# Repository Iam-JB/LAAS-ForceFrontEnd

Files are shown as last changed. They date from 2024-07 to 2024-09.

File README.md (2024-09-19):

# LAAS-ForceFrontEnd

Electronics development to acquire and process force measurements produced by an actuator in order to achieve torque control.

Here you will find the technical review : Technical Review and the poster here : Poster

Files sumarry :  
   ADS1235EVM.kicad_sch   KiCAD Schematic of our own acquisition PCB  
   ADS1235EVM.kicad_pcb   KiCAD PCB Routing of our own acquisition PCB  
   ForceDetection.ino       Code in order to flash Raspberry Pi Pico  
   ExtractData.py               Parceur that extracts force value from an external file ('xxx.bin') and plots through MatPlotLib  
   RealTimeParceur.py       Parceur that extracts data directly from serial port and plots through PlotJuggler

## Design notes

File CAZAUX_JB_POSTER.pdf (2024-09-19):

CONTEXTE
L’équipe Gepetto du LAAS CNRS à Toulouse travaille à la conception, à la génération de mouvement et au contrôle de robots à jambes (humanoides et quadrupède). Pour des besoins de retour d’effort et d’interaction souple avec l’environnement, les articulations des robots sont généralement équipées de capteurs de couple à base de jauge de contraintes. Une fois conditionnées et filtrées, les mesures de couples sont utilisées comme retour d’état du contrôleur du robot. L’équipe Gepetto juge essentiel la qualité de ces mesures d’effort dont dépend la stabilité et la robustesse de l’exécution des taches robotiques (locomotion, manipulation).
Ce stage vise à développer l’électronique pour acquérir et traiter les mesures de forces produites par un actionneur, afin de l’asservir en couple.

## MESURE DE LA FORCE APPLIQUÉE PAR UN ACTIONNEUR POUR LA RÉALISATION D’UN ASSERVISSEMENT MOTEUR EN COUPLE

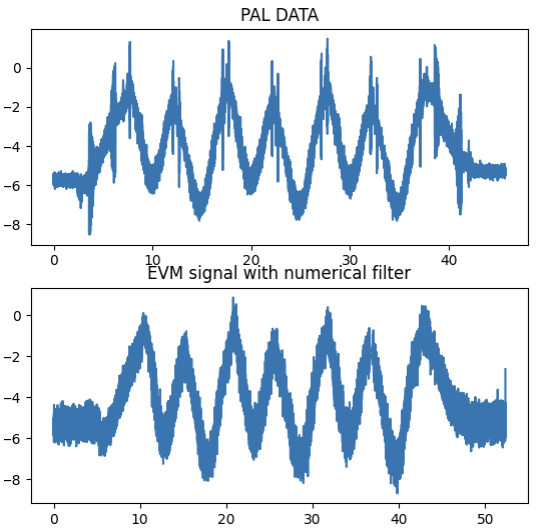
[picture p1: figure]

Jean-Baptiste Cazaux, 4°AE-SE

Mouvement des systèmes anthropomorphes

CONTRIBUTEURS
Thomas Flayols

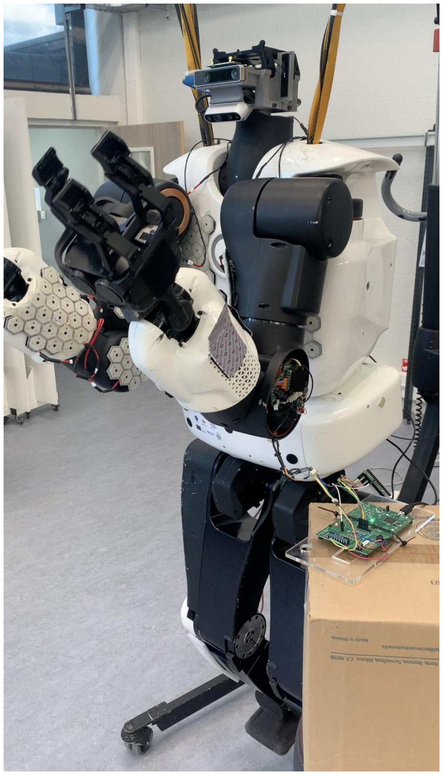
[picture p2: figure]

Jérome Manhes | Stéphane Grondin | Pierre Fernbach
CONCLUSION & PERSPECTIVES | APPORTS PERSONNELS

PROJET
Chaîne d’acquisition ratiométrique d’un pont de Wheatstone

### 1. Conception

### 2. Réalisation

### 3. Caractérisation

https://github.com/Iam-JB/LAAS-ForceFrontEnd

Recherche d’une solution générique permettant l’amplification différentielle, le filtrage et la conversion analogique numérique.
Schématique et routage de la carte d’acquisition.

Formation câblage et wrappage à l’atelier électronique et soudure de notre PCB avec des composants passifs en 0402.
Réalisation de parseurs en python et code pour commander divers microcontrôleurs (RPi 400, Pi Pico, ESP32).

Évaluation du niveau de bruit entre PCB et EVM (SNR, FFT).
Évaluation de la vitesse de communication UART. Comparaison avec l’amplificateur de PAL Robotics. Réalisation d’un filtre numérique et mise à l’échelle.

L’objectif du stage a été atteint avec l’implémentation d’une commande simple sur TALOS, servant de preuve de concept au fonctionnement de la carte d’acquisition.

Perspectives: Excitation AC et NTC pour le pont de jauges.

Ce stage m’a permis de me familariser avec le monde de la recherche ainsi que de mener à bien, en autonomie, un projet dans sa globalité.

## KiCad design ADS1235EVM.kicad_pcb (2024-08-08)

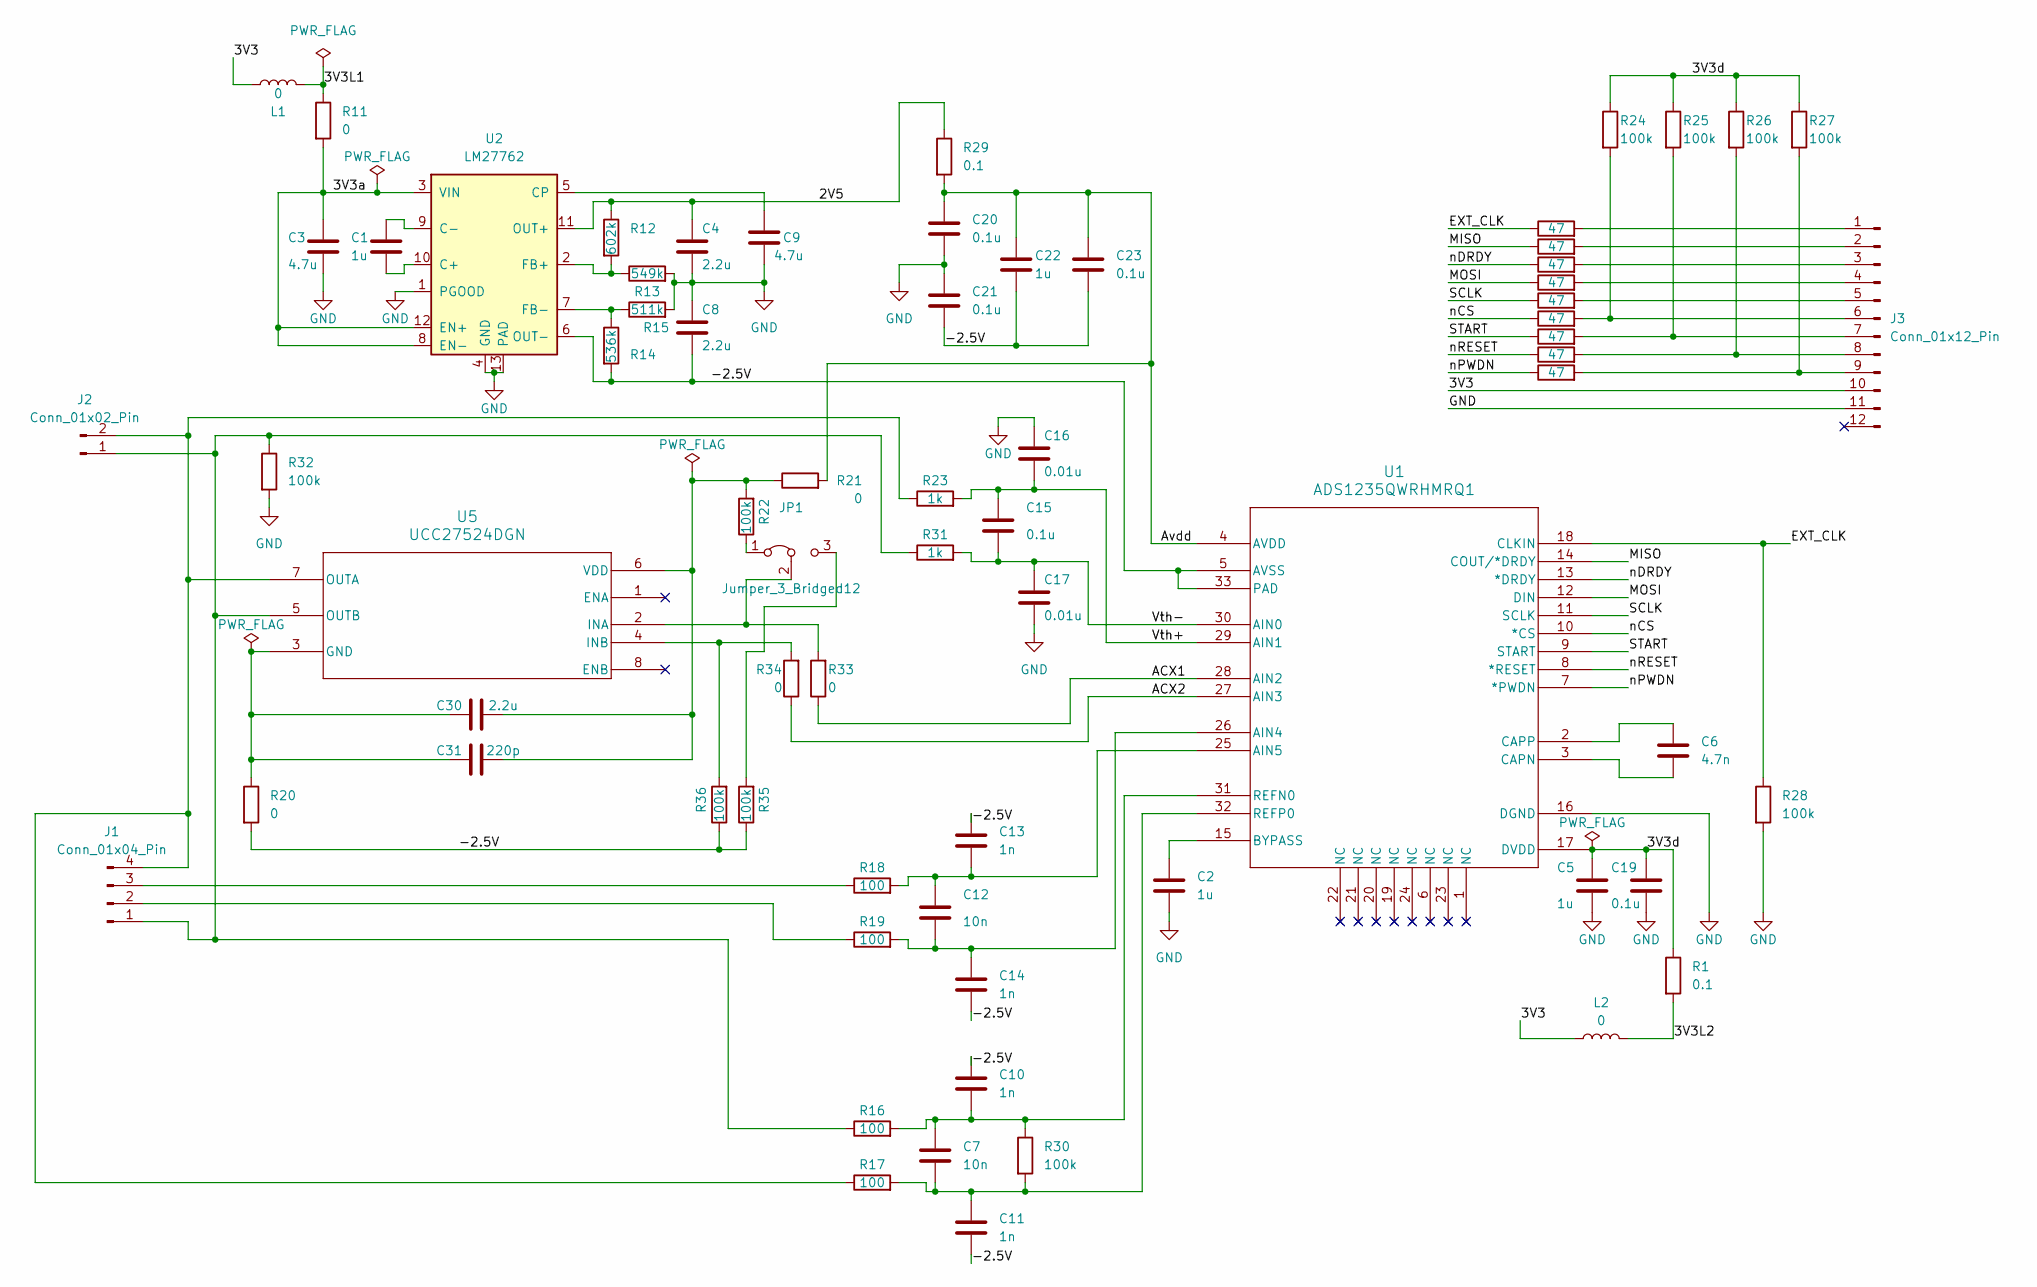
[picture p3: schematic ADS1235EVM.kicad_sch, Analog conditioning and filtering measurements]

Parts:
C1, C2, C5, C22: 1u; C_0402_1005Metric
C3, C9: 4.7u; C_0402_1005Metric
C4, C8, C30: 2.2u; C_0402_1005Metric
C6: 4.7n; C_0402_1005Metric
C7, C12: 10n; C_0402_1005Metric
C10, C11, C13, C14: 1n; C_0402_1005Metric
C15, C19, C20, C21, C23: 0.1u; C_0402_1005Metric
C16, C17: 0.01u; C_0402_1005Metric
C31: 220p; C_0402_1005Metric
J1: Conn_01x04_Pin; Hirose_DF13-04P-1.25DSA_1x04_P1.25mm_Vertical
J2: Conn_01x02_Pin; Hirose_DF13-02P-1.25DSA_1x02_P1.25mm_Vertical
J3: Conn_01x12_Pin; PinHeader_2x06_P2.54mm_Vertical
JP1: Jumper_3_Bridged12; SolderJumper-3_P1.3mm_Open_RoundedPad1.0x1.5mm
L1, L2: 0; L_0402_1005Metric
R1, R29: 0.1; R_0402_1005Metric
R2, R3, R4, R5, R6, R7, R8, R9, R10: 47; R_0402_1005Metric
R11, R20, R21, R33, R34: 0; R_0402_1005Metric
R12: 602k; R_0402_1005Metric
R13: 549k; R_0402_1005Metric
R14: 536k; R_0402_1005Metric
R15: 511k; R_0402_1005Metric
R16, R17, R18, R19: 100; R_0402_1005Metric
R22, R24, R25, R26, R27, R28, R30, R32, R35, R36: 100k; R_0402_1005Metric
R23, R31: 1k; R_0402_1005Metric
U1: ADS1235QWRHMRQ1; RHM0032A_VQFNP_TEX
U2: LM27762; WSON-12-1EP_3x2mm_P0.5mm_EP1x2.65_ThermalVias
U5: UCC27524DGN; DGN8

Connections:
/2V5: C4.1, R12.1, R29.1, U2.11 (OUT+)
/3V3: J3.10, L1.1, L2.1
/3V3L1: L1.2, R11.1
/3V3L2: L2.2, R1.2
/3V3a: C3.1, R11.2, U2.3 (VIN), U2.8 (EN-), U2.12 (EN+)
/3V3d: C5.1, C19.1, R1.1, R24.1, R25.1, R26.1, R27.1, U1.17 (DVDD)
/-2.5V: C8.2, C10.1, C11.2, C13.1, C14.2, C21.2, C22.2, C23.2, R14.2, R20.2, R35.1, R36.1, U1.5 (AVSS), U1.33 (PAD), U2.6 (OUT-)
/ACX1: R33.1, U1.28 (AIN2)
/ACX2: R34.1, U1.27 (AIN3)
/Avdd: C20.1, C22.1, C23.1, R21.2, R29.2, U1.4 (AVDD)
/EXT_CLK: R7.1, R28.1, U1.18 (CLKIN)
/MISO: R3.1, U1.14 (COUT/*DRDY)
/MOSI: R4.1, U1.12 (DIN)
/SCLK: R5.1, U1.11 (SCLK)
/START: R9.1, U1.9 (START)
/Vth+: C15.1, C16.2, R23.2, U1.29 (AIN1)
/Vth-: C15.2, C17.1, R31.2, U1.30 (AIN0)
/nCS: R6.1, U1.10 (*CS)
/nDRDY: R2.1, U1.13 (*DRDY)
/nPWDN: R10.1, U1.7 (*PWDN)
/nRESET: R8.1, U1.8 (*RESET)
GND: C2.2, C3.2, C4.2, C5.2, C8.1, C9.2, C16.1, C17.2, C19.2, C20.2, C21.1, J3.11, R13.2, R15.2, R28.2, R32.2, U1.16 (DGND), U2.1 (PGOOD), U2.4 (GND), U2.13 (PAD)
unnamed: J1.1, J2.1, R16.1, R31.1, R32.1, U5.5 (OUTB)
unnamed: J1.2, R19.1
unnamed: J1.3, R18.1
unnamed: J1.4, J2.2, R17.1, R23.1, U5.7 (OUTA)
unnamed: J3.1, R7.2
unnamed: J3.2, R3.2
unnamed: J3.3, R2.2
unnamed: J3.4, R4.2
unnamed: J3.5, R5.2
unnamed: J3.6, R6.2, R24.2
unnamed: J3.7, R9.2, R25.2
unnamed: J3.8, R8.2, R26.2
unnamed: J3.9, R10.2, R27.2
unnamed: JP1.1 (A), R22.1
unnamed: JP1.3 (B), R35.2
unnamed: JP1.2 (C), R33.2, U5.2 (INA)
unnamed: C12.2, C14.1, R19.2, U1.26 (AIN4)
unnamed: C12.1, C13.2, R18.2, U1.25 (AIN5)
unnamed: C2.1, U1.15 (BYPASS)
unnamed: C6.1, U1.3 (CAPN)
unnamed: C6.2, U1.2 (CAPP)
unnamed: C7.1, C10.2, R16.2, R30.1, U1.31 (REFN0)
unnamed: C7.2, C11.1, R17.2, R30.2, U1.32 (REFP0)
unnamed: C1.2, U2.10 (C+)
unnamed: C1.1, U2.9 (C-)
unnamed: C9.1, U2.5 (CP)
unnamed: R12.2, R13.1, U2.2 (FB+)
unnamed: R14.1, R15.1, U2.7 (FB-)
unnamed: C30.1, C31.1, R20.1, U5.3 (GND)
unnamed: R34.2, R36.2, U5.4 (INB)
unnamed: C30.2, C31.2, R21.1, R22.2, U5.6 (VDD)

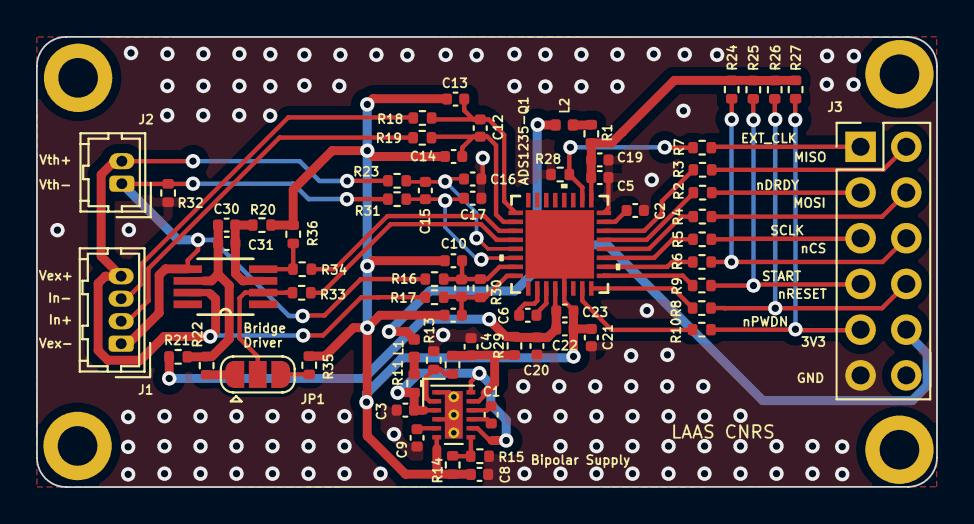
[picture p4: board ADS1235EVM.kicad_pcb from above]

Board: 2 copper layers, 50.0 x 25.0 mm, 69 parts (0 on the bottom side), 53 nets.

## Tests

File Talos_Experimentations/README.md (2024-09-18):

In this folder you will find all the results concerning differents experimentations of TALOS's left elbow torque sensor.

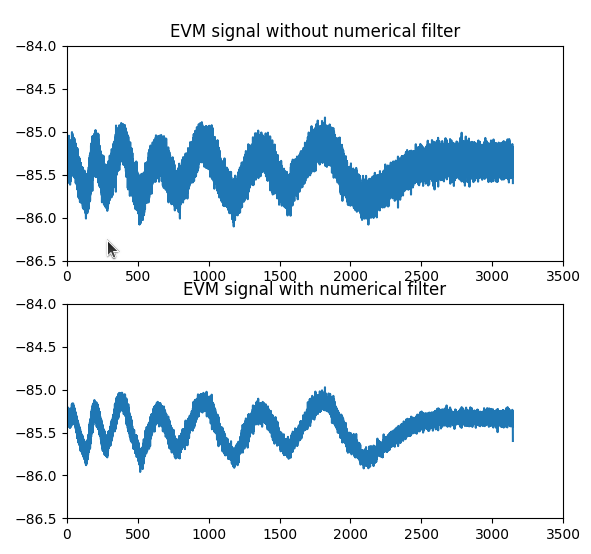
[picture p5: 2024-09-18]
Talos_Experimentations/EVM_with&withoutFilter+2kSAMPL.png

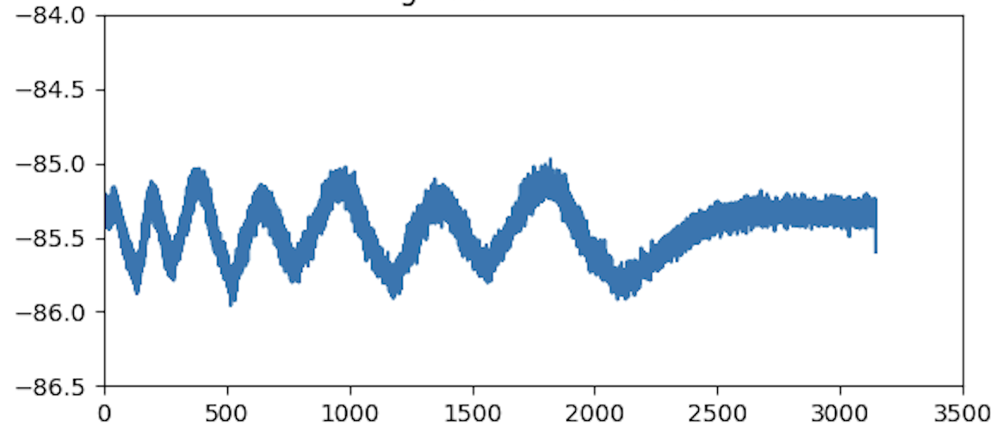
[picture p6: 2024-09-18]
Talos_Experimentations/EVM_FIltering+2kHzSampling.png

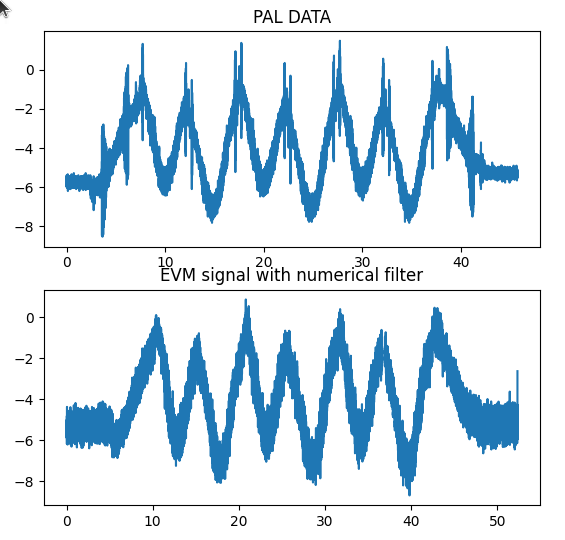
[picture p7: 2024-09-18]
Talos_Experimentations/comparaisonWithPAL_scaled.png

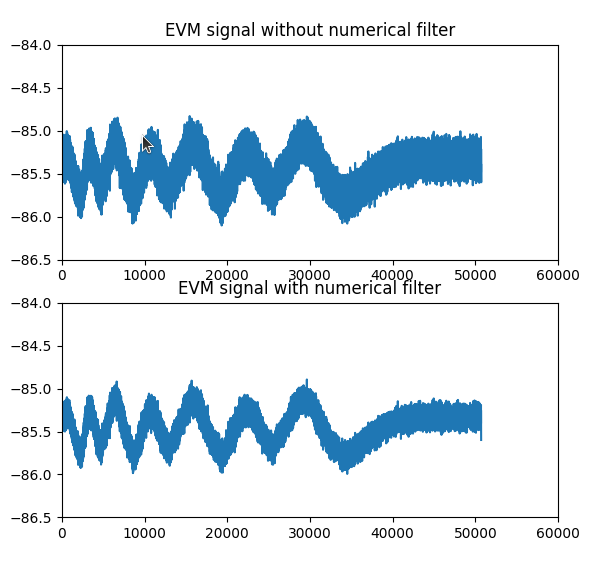
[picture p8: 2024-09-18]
Talos_Experimentations/EVM_with&withoutFilter.png

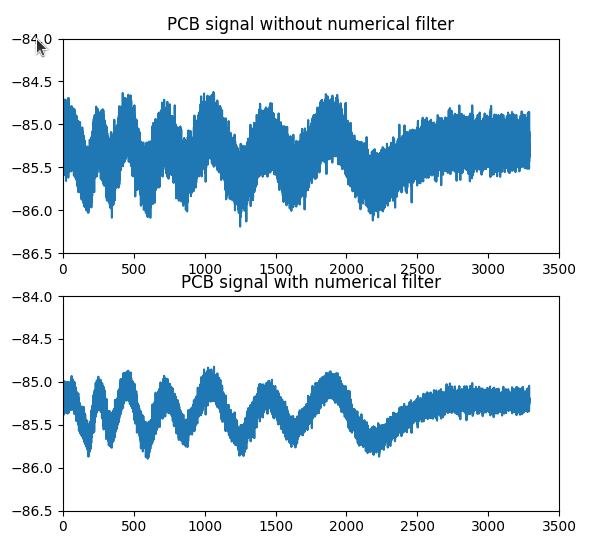
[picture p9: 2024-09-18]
Talos_Experimentations/PCB_with&withoutFilter+2kSAMPL.png

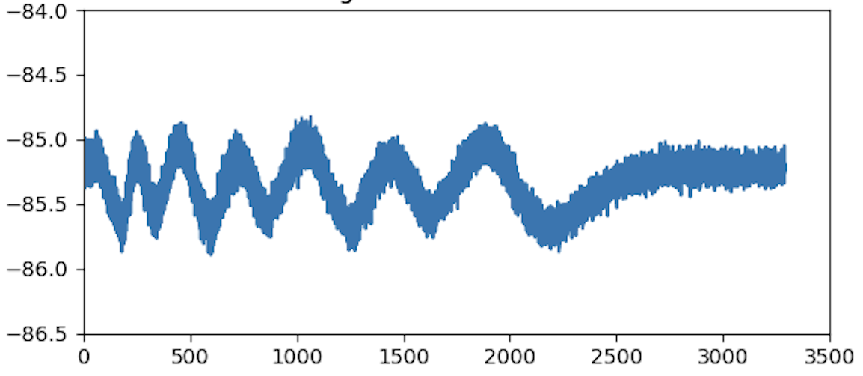
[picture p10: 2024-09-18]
Talos_Experimentations/PCB_Filtering+2kHzSampling.png

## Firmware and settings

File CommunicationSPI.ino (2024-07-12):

// For televersing the arduino code on the card
//    --> In order to solve the ttyACM0 probelm, you have to double-click the arduino reset button and then it goes fine

// I am currently blocked at the isTransferDone function
// @TO DO Check what SERCOM is necessary for implementing SPI on the Arduino Nano 33 IoT
//        Learn more about the Direct Access Memory (DMA)


#include <SPI.h>
#include <Adafruit_ZeroDMA.h>
#include "utility/dma.h"
#include "wiring_private.h" // pinPeripheral() function

#define nCS 8       // Chip Select
#define MOSI 11     // Master To Slave
#define MISO 12     // Slave To Master
#define SCLK 13     // Serial Clock

#define START 14
#define nDRDY 15
#define nPWDN 16
#define nRESET 17

SPIClassSAMD mySPI(
  &sercom1,
  12,
  13,
  11,
  SPI_PAD_0_SCK_1,
  SERCOM_RX_PAD_3
);

// MY VARIABLES

long ADC_VALUE;
long CLK = 7372800;      // 7.3728 MHz

Adafruit_ZeroDMA myDMA;
ZeroDMAstatus    stat;   // DMA status codes returned by some functions
DmacDescriptor *desc;    // DMA descriptor address

#define DATA_LENGTH 3
uint8_t receiveBuffer[DATA_LENGTH];
volatile bool isTransferDone = false;

// Callback for end of DMA transfer
void dmaCallback(Adafruit_ZeroDMA *dma) {
  (void) dma ;
  isTransferDone = true ;
  Serial.println("CALLBACK");
}

// Interrupt Service Routine for nDRDY
void nDRDY_ISR() {
  Serial.println("ENTRERING DATA READY HANDLER");

  digitalWrite(nCS, LOW);
  
  while (!isTransferDone) {                  // I am blocked here !! The callback function is never called
    
    if (myDMA.isActive()) {
      Serial.println("DR HANDLER : The transfer is still being processed...");
    } else {
      Serial.println("DR HANDLER : The transfer isn't in processing mode");
    }

    // print the register in order to know if it is my configuration that isn't good or smthing else
    
    delay(1000000);
  }
  Serial.println("DR HANDLER : The transfer is finally finished !");

  // Process received data
  ADC_VALUE = 0;
  for (int i = 0; i < DATA_LENGTH; i++) {
    ADC_VALUE = (ADC_VALUE << 8) | receiveBuffer[i];
  }

  Serial.print("ADC VALUE: ");
  Serial.println(ADC_VALUE);

  isTransferDone = false;

  stat = myDMA.free();
  if (stat != DMA_STATUS_OK) {
    Serial.println("DMA free has failed");
  }

  stat = myDMA.allocate();
  if (stat != DMA_STATUS_OK) {
    Serial.println("DMA allocate has failed");
    myDMA.printStatus(stat);
  }
  
  stat = myDMA.startJob();
  if (stat != DMA_STATUS_OK) {
    Serial.println("DMA start has failed");
    myDMA.printStatus(stat);
  }
  
  digitalWrite(START, HIGH);                // Start or restart a new ADC conversion
  digitalWrite(nCS, HIGH);
}


// MY FUNCTIONS

void initArduinoNano() {
  pinMode(nCS,    OUTPUT);
  pinMode(MOSI,   OUTPUT);
  pinMode(MISO,   INPUT );
  pinMode(SCLK,   OUTPUT);
  pinMode(START,  OUTPUT);
  pinMode(nRESET, OUTPUT);
  pinMode(nPWDN,  OUTPUT);
  pinMode(nDRDY,  INPUT );

  pinPeripheral(MOSI, PIO_SERCOM);
  pinPeripheral(MISO, PIO_SERCOM);
  pinPeripheral(SCLK, PIO_SERCOM);
}

int readRegister(byte address) {
  byte command = 0x20 + (address & 0x1F);  // RREG is 20h + rrh where rrh is a 5-bit register address
  digitalWrite(nCS, LOW);                                   
  mySPI.transfer(command);                   // BYTE 1 (DIN : 0x20 + 5-bit register address, DOUT : 0xFF)
  mySPI.transfer(0xFF);                      // BYTE 2 (DIN : Arbitary, DOUT : Echo byte 1)
  int value = mySPI.transfer(0x00);          // BYTE 3 (DIN : 0x00, DOUT : Register data)
  digitalWrite(nCS, HIGH);
  return value;
}

void writeRegister(byte address, int value) {
  digitalWrite(nCS, LOW);  
  byte command = 0x40 + address;
  mySPI.transfer(command);                // BYTE 1 (DIN : 0x40 + 5-bit register address, DOUT : 0xFF)
  mySPI.transfer(value);                  // BYTE 2 (DIN : Register data, DOUT : Echo byte 1)
  digitalWrite(nCS, HIGH);
}

void setup() {
  Serial.begin(2000000);
  while(!Serial);
  Serial.println("HELLO WORLD");
  initArduinoNano();

  mySPI.begin(); // Initialize the SPI library
  mySPI.beginTransaction(SPISettings(8000000, MSBFIRST, SPI_MODE1));

  digitalWrite(nCS, HIGH); // Communication disable
  digitalWrite(nRESET, HIGH);
  digitalWrite(nPWDN, HIGH);

  // OPTIONAL : AC EXCITATION
  
//  byte address = 0x03 ;
//  byte value = readRegister(address);

//  value &= ~((0b11) << 5); // Clear the bits of CHOP[1:0]
//  value |= (0b10 << 5);    // 2-wire AC-bridge excitation mode

//  writeRegister(address,value);

  // DATA RATE CONFIGURATION
  byte addressDR = 0b00010;
  int valueDR = readRegister(addressDR);
  valueDR = 0b01100100;
  writeRegister(addressDR, valueDR);

  // PGA CONFIGURATION
  byte addressPGA = 0b10000;
  int valuePGA = readRegister(addressPGA);
  valuePGA = 0b10000111;  // Gain of 128
  writeRegister(addressPGA, valuePGA);

  // INPUT MUX CONFIGURATION
  byte addressMUX = 0b10001;
  int valueMUX = readRegister(addressMUX);
  valueMUX = 0b01111000;
  writeRegister(addressMUX, valueMUX);

  // REF CONFIGURATION
  byte addressREF = 0b00110;
  int valueREF = readRegister(addressREF);
  valueREF = 0b00001010;
  writeRegister(addressREF, valueREF);

  // OFFSET CALIBRATION
  writeRegister(0x07, 0x00);
  writeRegister(0x08, 0x00);
  writeRegister(0x09, 0x00);

  // FULL SCALE CALIBRATION
  writeRegister(0x0A, 0x00);
  writeRegister(0x0B, 0x00);
  writeRegister(0x0C, 0x40);


  // Direct Access Memory (DMA)
  
  stat = myDMA.allocate();
  if (stat != DMA_STATUS_OK) {
    Serial.print("Allocate : ");
    myDMA.printStatus(stat);
  }

    // DMA Configuration for SPI    
             
        // SERCOM4 is the 'native' SPI SERCOM on most M0 boards but section 6. mentions that according to the Arduino pinout,
        // the SERCOM that corresponds is the SERCOM1
        
  myDMA.setTrigger(SERCOM1_DMAC_ID_RX);       // To receive from SPI
  Serial.print("TRIGGER bit : ");
  Serial.println(DMAC->CHCTRLB.bit.TRIGSRC);
  myDMA.setAction(DMA_TRIGGER_ACTON_BEAT);
  Serial.print("ACT ON bit : ");
  Serial.println(DMAC->CHCTRLB.bit.TRIGACT);

  desc = myDMA.addDescriptor(
    (void *)(&SERCOM1->SPI.DATA.reg),   // SRC
    receiveBuffer,                      // DEST
    DATA_LENGTH,                        // length
    DMA_BEAT_SIZE_BYTE,                 // bytes
    false,                              // no incrementation of SRC address
    true                                // incrementation of DEST address
  );

    // Fill the buffer with incrementing bytes
//  for (uint32_t i=0; i<DATA_LENGTH; i++) {       // Does that is really usefull here ? Why's that ?
//    receiveBuffer[i]=i;
//  }

  myDMA.loop(false);
  myDMA.setCallback(dmaCallback, DMA_CALLBACK_TRANSFER_DONE);            // The second argument (DMA_CALLBACK_TRANSFER_DONE) is not especially necessary here as it is set by default
  myDMA.setPriority(DMA_PRIORITY_3);         // Set the highest to DMA
 
    // Enable global interrupts
  NVIC_SetPriority(DMAC_IRQn, 10);           // Set the Nested Vector Interrupt Controller (NVIC) priority for the DMAC to 0 (highest) 
  NVIC_EnableIRQ(DMAC_IRQn);
  
    // Attach interrupt to nDRDY pin
  attachInterrupt(digitalPinToInterrupt(nDRDY), nDRDY_ISR, FALLING);

  stat = myDMA.startJob();
  if (stat != DMA_STATUS_OK) {
    Serial.println("DMA start has failed");
    myDMA.printStatus(stat);
  }

  digitalWrite(nCS, LOW);             // Enable communication
  digitalWrite(START, HIGH);          // ADC start
  Serial.println("I've been here");
}

void loop() {
  // Nothing here, done by IT
  
  Serial.println(".");
  
//  Serial.print("enable bit : ");
//  Serial.println(DMAC->CHCTRLA.bit.ENABLE);
//
//  Serial.print("Transfer Complete bit : ");
//  Serial.println(DMAC->CHINTFLAG.reg);
//
//  Serial.print("Chanel causing IT : ");
//  Serial.println(DMAC->INTPEND.bit.ID);
}

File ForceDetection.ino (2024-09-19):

#include <stdio.h>
#include <SPI.h>

// Jean-Baptiste CAZAUX - Tuesday 16 July
// https://github.com/Iam-JB/LAAS-ForceFrontEnd

// GPIOs DEFINITION
const int nCS = 17;
const int START = 20;
const int nDRDY = 21;
const int nPWDN = 26;
const int nRESET = 22;

// Buffers
const int SYNC = 0x31;
uint16_t counter = 0x0000;      // Counter 16 bits
uint8_t tabToBeSendUART[6];

void initPiPico() {
    // Initialize GPIO pins
    pinMode(nCS, OUTPUT);
    pinMode(START, OUTPUT);
    pinMode(nRESET, OUTPUT);
    pinMode(nPWDN, OUTPUT);
    pinMode(nDRDY, INPUT);

    // Initialize SPI
    SPI.begin();
    SPI.beginTransaction(SPISettings(4000000,MSBFIRST,SPI_MODE1));
}

// READ ADS1235Q1's REGISTERS
uint8_t readRegister(uint8_t address) {
    uint8_t command = 0x20 + (address & 0x1F); // RREG is a 0x20 + rrh, where rrh is a 5-bit register
    digitalWrite(nCS, LOW);
    SPI.transfer(command);
    SPI.transfer(0xFF);
    uint8_t value = SPI.transfer(0x00);
    digitalWrite(nCS, HIGH);
    return value;
}

// WRITE ADS1235Q1's REGISTERS
void writeRegister(uint8_t address, uint8_t value) {
    digitalWrite(nCS, LOW);
    uint8_t command = 0x40 + (address & 0x1F); // WREG is a 0x40 + rrh, where rrh is a 5-bit register
    SPI.transfer(command);
    SPI.transfer(value);
    digitalWrite(nCS, HIGH);
}

void setupMain() {
    // INIT
    Serial.begin();   // No need to specify serial speed for Pi Pico due to virtual UART
    while(!Serial);
    initPiPico();

    digitalWrite(nCS, HIGH);
    digitalWrite(nRESET, HIGH);
    digitalWrite(nPWDN, HIGH);
    digitalWrite(START, LOW);

    // DC-EXCITATION CONFIGURATION
    uint8_t addressEXC = 0b00011;
    uint8_t valueDC = 0b00001001;  // DC-EXCITATION and conversion start delay = 1.16ms (cf. datasheet)
    writeRegister(addressEXC, valueDC);

    // DATA RATE CONFIGURATION
    uint8_t addressDR = 0b00010;
//    uint8_t valueDR = 0b01100011;  // 7200 SPS & sinc1 (-3dB cutoff frequency at 2300Hz)
//    uint8_t valueDR = 0b01100011;  // 7200 SPS & sinc2 (-3dB cutoff frequency at 1960Hz)
//    uint8_t valueDR = 0b01100011;  // 7200 SPS & sinc3 (-3dB cutoff frequency at 1740Hz)
    uint8_t valueDR = 0b01100011;  // 7200 SPS & sinc4 (-3dB cutoff frequency at 1580Hz)
    writeRegister(addressDR, valueDR);

    // PGA CONFIGURATION
    uint8_t addressPGA = 0b10000;
    uint8_t valuePGA = 0b10000111;  // Gain of 128
    writeRegister(addressPGA, valuePGA);

    // INPUT MULTIPLEXER CONFIGURATION
    uint8_t addressMUX = 0b10001;
    uint8_t valueMUX = 0b01111000;  // AIN4(+) and AIN5(-)
    writeRegister(addressMUX, valueMUX);

    // REFERENCE CONFIGURATION
    uint8_t addressREF = 0b00110;
    uint8_t valueREF = 0b00001010;
    writeRegister(addressREF, valueREF);

    // USER CALIBRATION
       // OFCAL
    // writeRegister(0x07, 0x00); // Follow the user calibration procedure (cf. datasheet)
    // writeRegister(0x08, 0x00);
    // writeRegister(0x09, 0x00);
    writeRegister(0x07, 0x7D); // Follow the user calibration procedure (cf. datasheet)
    writeRegister(0x08, 0x27);
    writeRegister(0x09, 0x04);

      // FSCAL
    writeRegister(0x0A, 0x00); // Follow the user calibration procedure (cf. datasheet)
    writeRegister(0x0B, 0x00);
    writeRegister(0x0C, 0x40);
  //  writeRegister(0x0A, 0xCC);
  //  writeRegister(0x0B, 0xCC);
  //  writeRegister(0x0C, 0x3C);
}


void myCallback() {
    uint32_t ADC_VALUE = 0;
    
    digitalWrite(nCS, LOW);
    SPI.transfer(0x12);
    SPI.transfer(0xFF);
    uint8_t MSB = SPI.transfer(0x00);
    uint8_t MIDSB = SPI.transfer(0x00);
    uint8_t LSB = SPI.transfer(0x00);
    digitalWrite(nCS, HIGH);

    int data[3] = {MSB,MIDSB,LSB};
    for (int i = 0 ; i <= 2 ; i++){
      ADC_VALUE = (ADC_VALUE << 8) | data[i];
    }
    uint32_t ADC_VALUE_DATA = ADC_VALUE & 0x7FFFFF ;
    uint32_t ADC_VALUE_SIGN = (ADC_VALUE & 0x800000) >> 23 ;

    // FORMATING AS SYNC | COUNTER | FORCE_VALUE
    counter++;
    uint8_t MSBcounter = (counter & 0xFF00) >> 8 ;
    uint8_t LSBcounter = counter & 0x00FF ;
    
    tabToBeSendUART[0] = SYNC ;
    tabToBeSendUART[1] = MSBcounter ;
    tabToBeSendUART[2] = LSBcounter ;
    tabToBeSendUART[3] = MSB ;
    tabToBeSendUART[4] = MIDSB ;
    tabToBeSendUART[5] = LSB ;

    Serial.write(tabToBeSendUART,6);
    Serial.flush();

    if (counter >= 0xFFFF) { // Not really needed here as counter is defined as a uint16_t
      counter = 0x0000;
    }

}

void setup() {
    setupMain();
    digitalWrite(START, HIGH); // Start conversion acquisitions
}

void loop() {
  while (1) {
    while(!digitalRead(nDRDY));
    while(digitalRead(nDRDY));
    myCallback();
  }
}

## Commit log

2024-06-19 Schematics - All components included
    [PrincipleSchematicV3.kicad_sch]
2024-06-19 Schematics - Add of jumpers to handle AC or DC excitation
    [PrincipleSchematicV4.kicad_sch]
2024-06-21 Double Side Routing - First version
    [PrincipleSchematicV4.kicad_pcb]
2024-06-21 Double Side Routing - Second version
    It is a more compact PCB with the add of a bottom ground surface
    [PrincipleSchematicV4bis.kicad_pcb]
2024-06-24 Project - Both the schematic and routing files included
2024-06-24 Add schematic & routing files
    [ADS1235EVM.kicad_pcb, ADS1235EVM.kicad_sch]
2024-06-24 Routing - Add of 2 ferrites bead for power
    [ADS1235EVM.kicad_pcb]
2024-06-25 Routing - Tie unused analog inputs to Avdd
    [ADS1235EVM.kicad_pcb]
2024-06-25 Routing - Components placement correction + DRC OK
    [ADS1235EVM.kicad_pcb]
2024-06-25 Add of .kicad_pro file
2024-06-25 Schematic - Jumpers removed + ERC OK
    [ADS1235EVM.kicad_sch]
2024-06-25 PCB - Add of net names
    [ADS1235EVM.kicad_pcb]
2024-06-25 PCB - Correction net names
    [ADS1235EVM.kicad_pcb]
2024-06-25 PCB - Add of components name
    [ADS1235EVM.kicad_pcb]
2024-06-25 PCB - Change of the ±Vref track size
    [ADS1235EVM.kicad_pcb]
2024-06-26 PCB - Add of 2 jumpers to handle AC & DC excitation
    [ADS1235EVM.kicad_pcb]
2024-06-26 Schematic - Add of 2 jumpers to handle AC & DC excitation
    [ADS1235EVM.kicad_sch]
2024-06-28 PCB - Components placement optimisation & add of GND vias
    [ADS1235EVM.kicad_pcb]
2024-07-01 Association Schematic & PCB
    [ADS1235EVM.kicad_pcb, ADS1235EVM.kicad_sch]
2024-07-01 Add Arduino file for SPI
2024-07-03 Arduino - First functional version
2024-07-03 Arduino - Correction of WREG and RREG bytes
    [CommunicationThroughSPI.ino]
2024-07-04 Add of 2.54mm SPI connector & open jumper
    [ADS1235EVM.kicad_pcb, ADS1235EVM.kicad_sch]
2024-07-05 Arduino - Delay deleted
2024-07-08 Arduino - Wait for serial connexion
2024-07-10 Arduino - Implementation of DMA and IT
2024-07-12 Arduino DMA - Update file
2024-07-22 RPi - Use of DMA
    Run the main .py script as root in order to have access to all peripherals
2024-07-24 RPi - Calibration in Newtons
    weight : 100g <-> adc code : 3150
2024-07-24 RPi - Noise RMS calculation
    [SPI_DMA.py]
2024-07-29 RPi - Add of ADC internal temperature calculation
2024-08-05 KiCAD - Change ferrite net names
    [ADS1235EVM.kicad_pcb, ADS1235EVM.kicad_sch]
2024-08-05 RPi - Correction of internal temperature measurement
    [SPI_DMA.py]
2024-08-08 KiCAD - Add of load cell measurement
    [ADS1235EVM.kicad_pcb, ADS1235EVM.kicad_sch]
2024-08-08 KiCAD - Adjustment of track width
    [ADS1235EVM.kicad_pcb]
2024-09-09 ESP32 - Conversion & Extraction values
2024-09-09 ESP32 - Comments modifications
2024-09-09 Pi Pico - Correction of counter bugs
    [ExtractData.py, ForceDetection.ino]
2024-09-10 Pi Pico - Calibration modifications
2024-09-10 Pi Pico - Add of counter tracking functionality
2024-09-11 Pi Pico - Correction of calibration procedure
    [ForceDetection.ino]
2024-09-11 Pi Pico - Take into account A2 complementary in the parseur
2024-09-13 Pi Pico - Delay deleted
2024-09-13 Pi Pico - Real-Time data extraction from serial
2024-09-19 Pi Pico - Functional version & Code well commented
2024-09-19 Pi Pico - Add of FFT plot
2024-09-19 Pi Pico - Print deleted
